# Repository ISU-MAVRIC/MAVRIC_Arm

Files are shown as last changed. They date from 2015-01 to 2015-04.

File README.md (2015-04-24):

# MAVRIC_Arm
The MAVRIC Arm consists of a rotating base (stepper motor), 'shoulder' actuator (with feedback), 'elbow' actuator (with feedback), and an end effector. The end effector is modular but at its maximum contains a rotation servo, horizontal servo, vertical servo, and gripping servo. This board interfaces with the MAVRIC main board, receiving control packets and sending back status packets.

**Features**
- 4 7.4V 5A Buck Regulators powering the high power end effector servos
  - Current measurement on every power output to prevent overheating of both the regulators and the servos themselves
- 3V3 and 5V Buck Regulators powering the STM32 and an external Raspberry Pi
- Powered by single 12V battery rail
- STM32 communicating over RS-485 with the MAVRIC main board for control/status transmission
- STM32 generating PWM to control the actuator drivers, servos, and stepper driver

## Arm Board Prototype 1 Ordered:
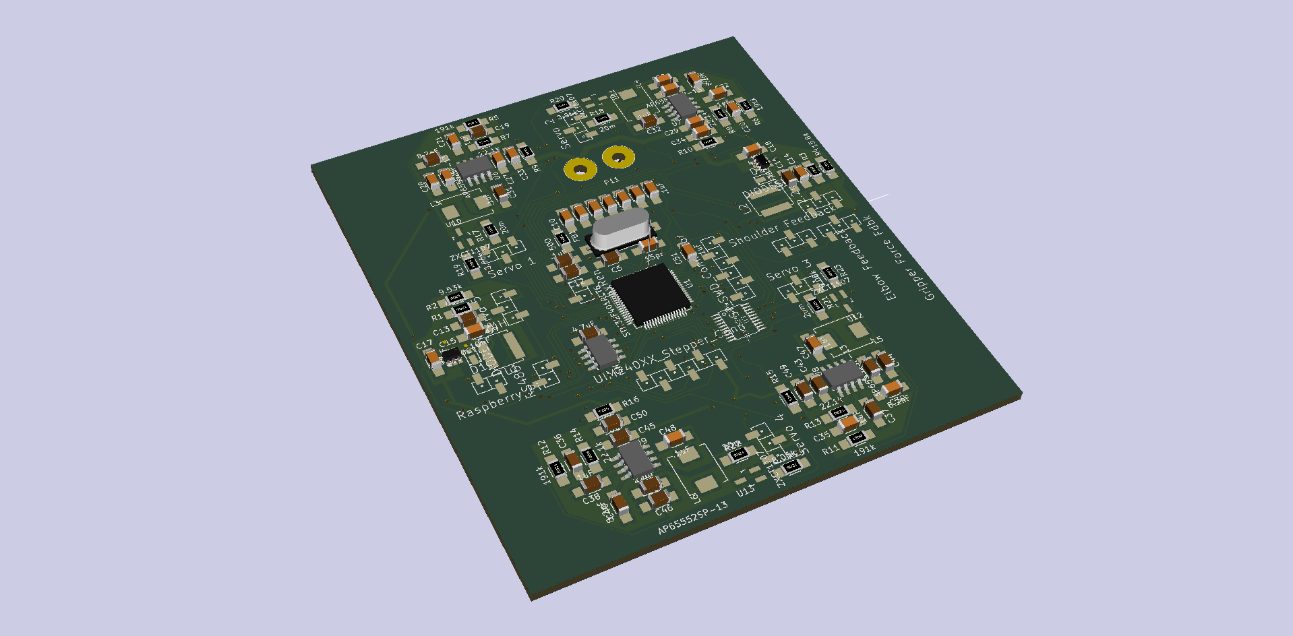
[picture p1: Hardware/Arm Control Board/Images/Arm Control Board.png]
Board 3D


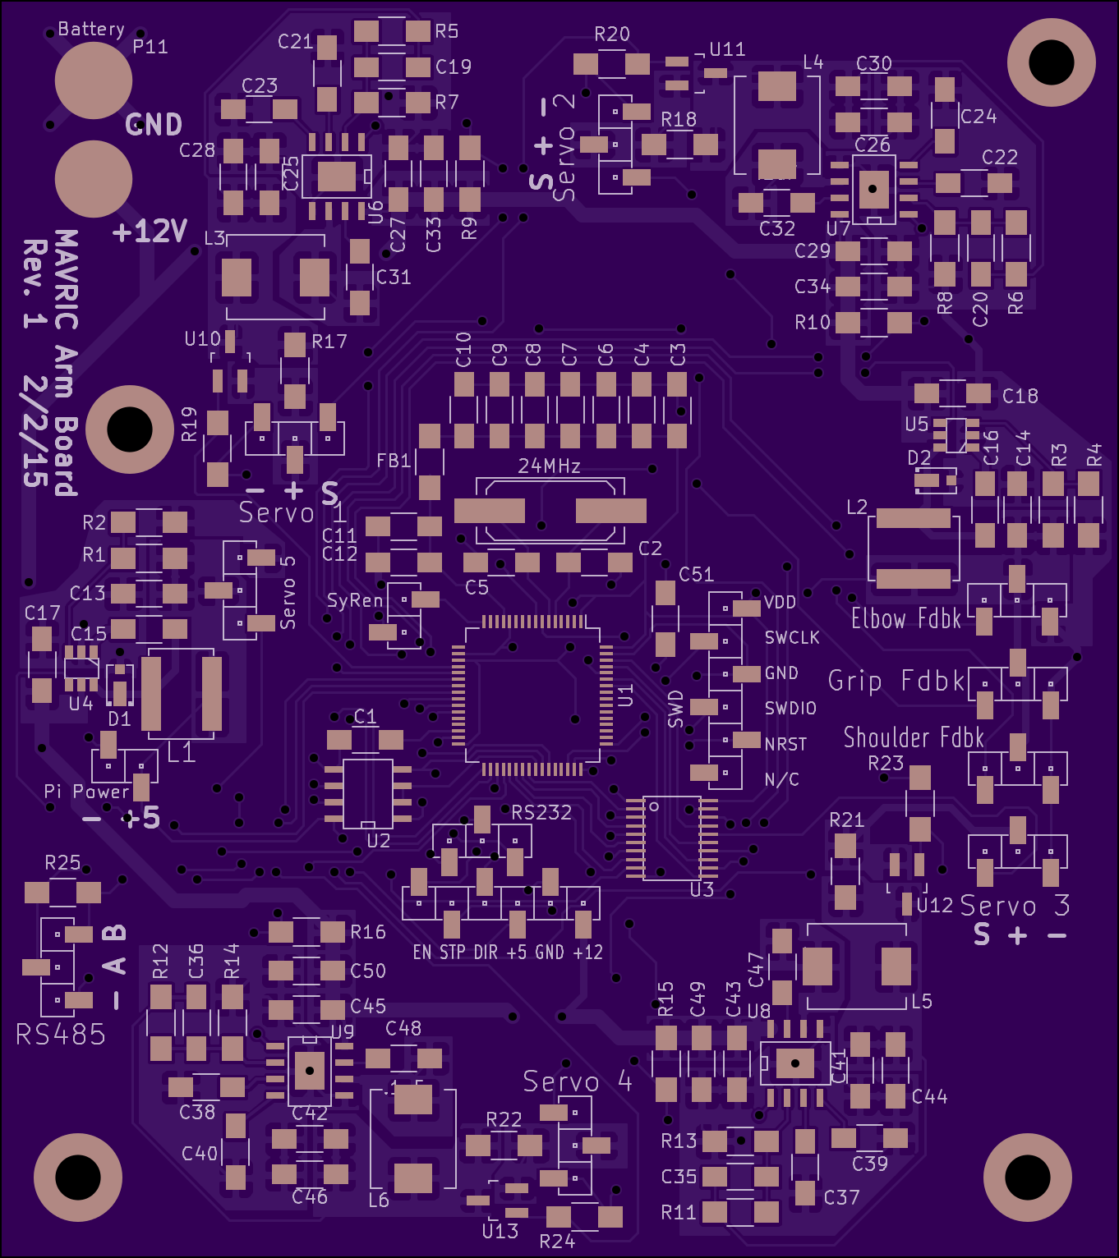
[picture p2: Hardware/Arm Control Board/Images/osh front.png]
Arm Board Front
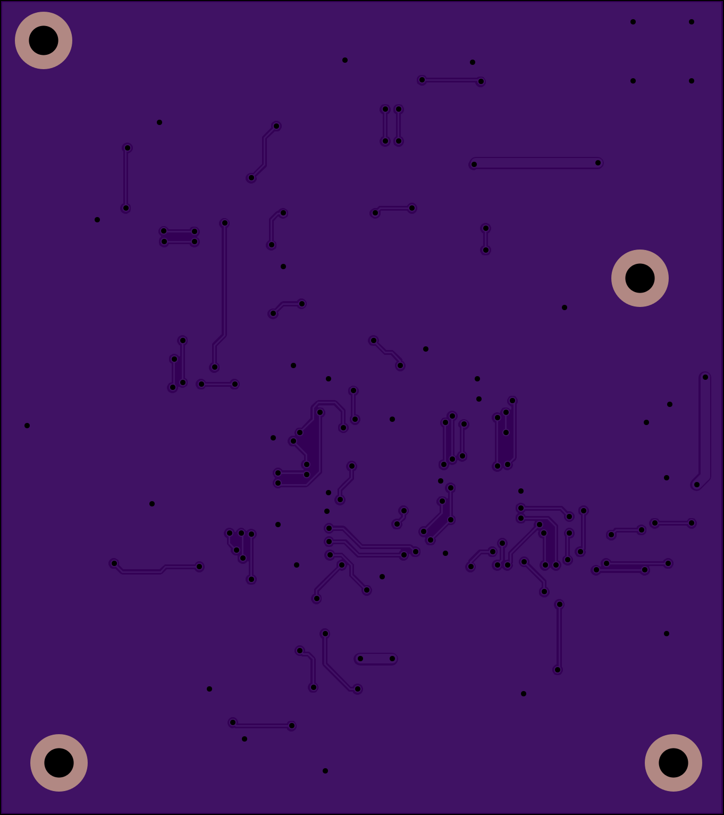
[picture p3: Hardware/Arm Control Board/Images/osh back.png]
Arm Board Back


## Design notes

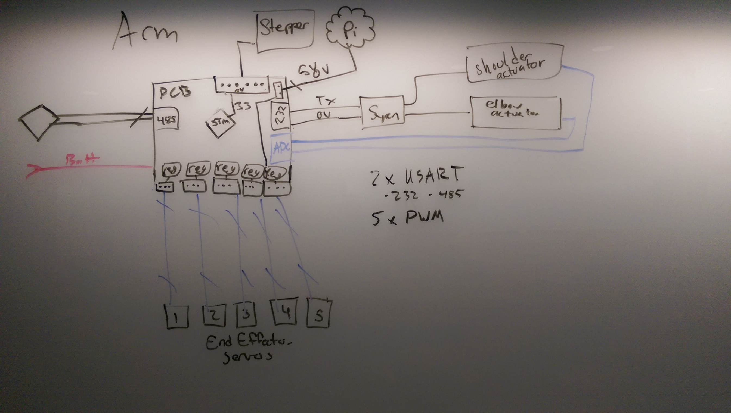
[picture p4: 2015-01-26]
Hardware/Whiteboard Layout.jpg

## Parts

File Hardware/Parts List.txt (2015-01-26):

*Micro*
STM32F401RCT6
*Regulator*
AZ34063UMTR-G1 (Only 1.2A)
AP65552SP-13 (5A sustained)
*RS485 Transceiver*
ST485CDR - More expensive
SN75176BDR - from TI, less expensive

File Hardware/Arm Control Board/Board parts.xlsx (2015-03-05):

Number | Qty | Description
952-1951-ND | 13 | 8POS SIL VERTICAL SMT HEADER
952-2001-ND | 2 | 8POS SIL VERTICAL SMT HEADER
97-14047-ND | 1 | IC MCU ARM M4 32BIT RISC 64LQFP
296-1275-1-ND | 1 | IC DIFF BUS TXCVR 8-SOIC
887-2439-1-ND | 1 | CRYSTAL 24.000MHZ 12PF SMD
568-8329-5-ND | 1 | IC BUFF/DVR TRI-ST DUAL 20TSSOP
AP65552SP-13DICT-ND | 4 | IC REG BUCK ADJ 5A SO-8
ZXCT1107SA-7DICT-ND | 4 | IC CURR MONITOR HIGH SIDE SOT23
785-1277-1-ND | 2 | IC REG BUCK ADJ 1.2A SOT23-6
240-2412-1-ND | 1 | FB1
1276-2854-1-ND | 12 | C3 C4 C6 C8 C9 C10 C11 C51 C31 C32 C47 C48
587-2254-1-ND | 4 | C7 C1 C18 C17
399-8148-1-ND | 5 | C12 C21 C22 C37 C38
887-2439-1-ND | 1 | X1
1276-2809-1-ND | 2 | C5 C2
P100ECT-ND | 1 | R25
MSS2P3-M3/89AGICT-ND | 2 | D2 D1
587-1353-1-ND | 10 | C14 C13 C27 C33 C29 C34 C43 C49 C45 C50
399-7174-1-ND | 2 | C16 C15
587-2098-1-ND | 2 | L2 L1
311-49.9KFRCT-ND | 2 | R3 R1
311-15.8KFRCT-ND | 1 | R4
311-9.53KFRCT-ND | 1 | R2
311-191KFRCT-ND | 4 | R5 R6 R11 R12
311-22.1KFRCT-ND | 4 | R7 R8 R13 R14
311-1152-1-ND | 4 | C19 C20 C35 C36
311-100KERCT-ND | 4 | R9 R10 R15 R16
311-1211-1-ND | 4 | C23 C24 C39 C40
1276-2728-1-ND | 8 | C28 C25 C30 C26 C44 C41 C46 C42
ASPI-0630LR-3R3M-T15CT-ND | 4 | L3 L4 L5 L6
985-1548-1-ND | 4 | R17 R18 R21 R22
P8.06KFCT-ND | 4 | R19 R20 R23 R24
 | 115

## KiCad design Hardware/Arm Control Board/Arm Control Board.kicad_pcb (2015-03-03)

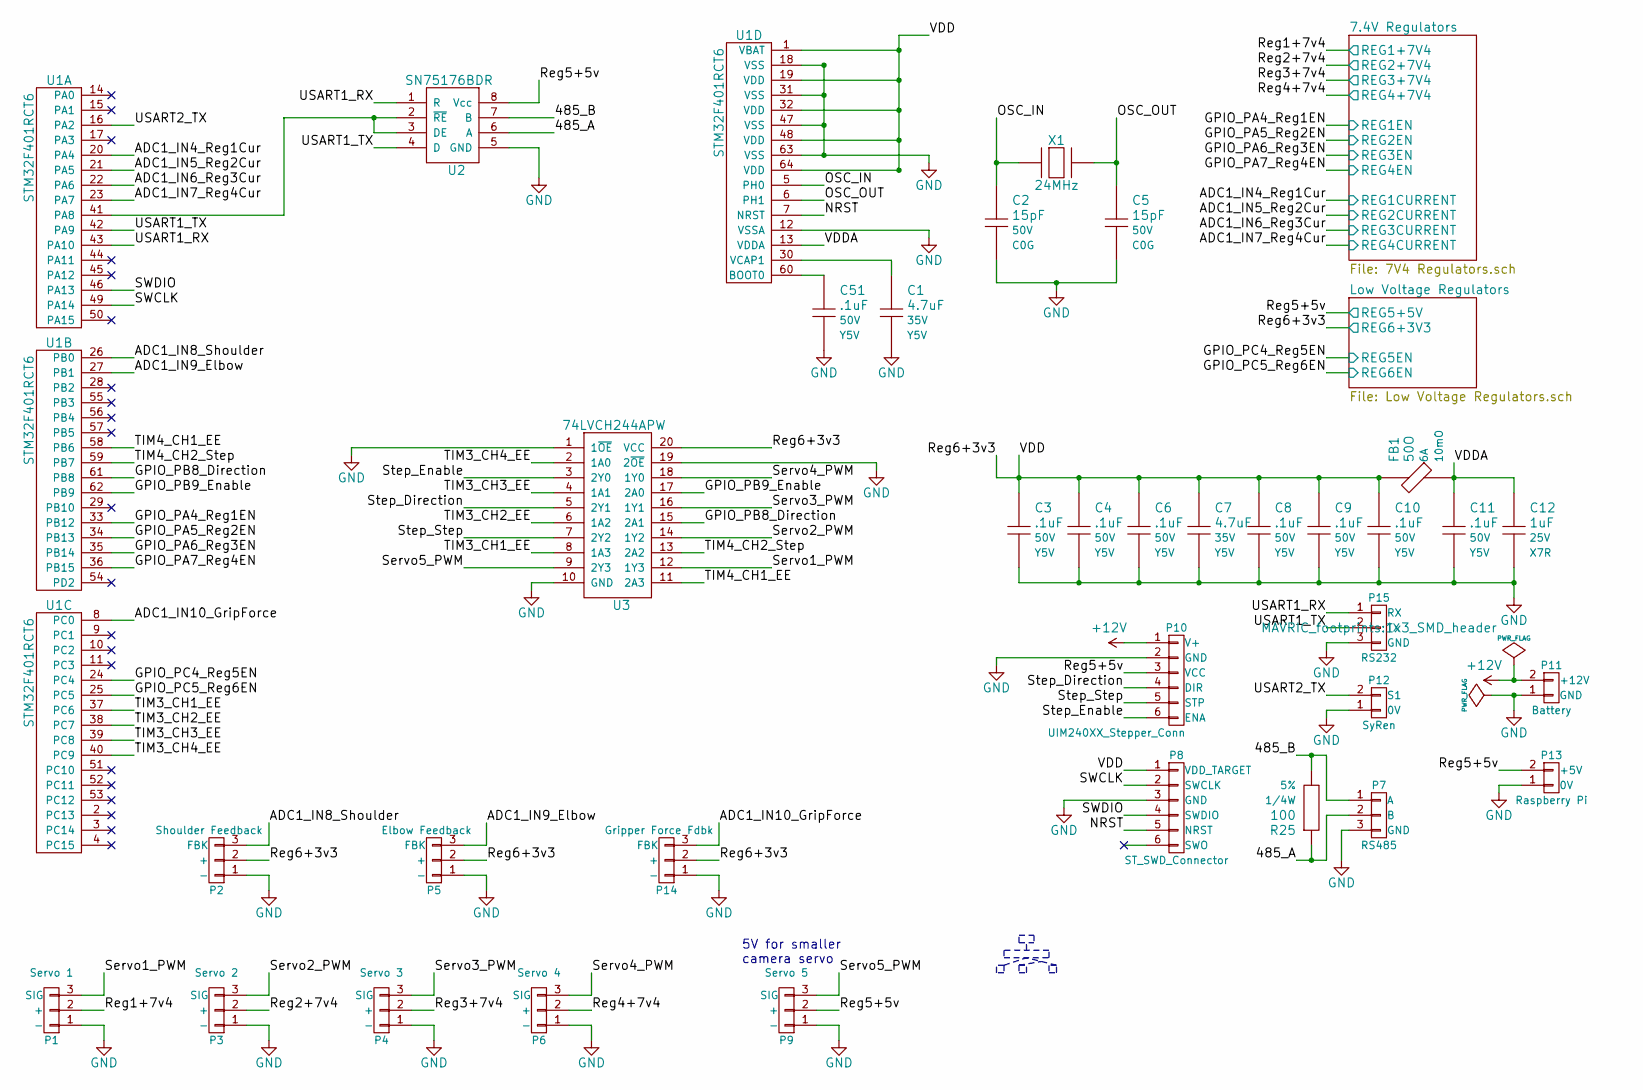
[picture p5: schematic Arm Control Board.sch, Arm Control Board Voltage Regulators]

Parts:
C1, C7: 4.7uF; C_1206_HandSoldering; Voltage 35V; Manufacturer Part # GMK316F475ZG-T
C2, C5: 15pF; C_1206_HandSoldering; Voltage 50V; Manufacturer Part # CL31C150JBCNNNC
C3, C4, C6, C8, C9, C10, C11, C51: .1uF; C_1206_HandSoldering; Voltage 50V; Manufacturer Part # CL31F104MBCNNNC
C12: 1uF; C_1206_HandSoldering; Voltage 25V; Manufacturer Part # C1206C105M3RACTU
FB1: 50O; R_1206_HandSoldering; Manufacturer Part # HI1206T500R-10
P1: Servo 1; 1x3_SMD_header
P2: Shoulder Feedback; 1x3_SMD_header
P3: Servo 2; 1x3_SMD_header
P4: Servo 3; 1x3_SMD_header
P5: Elbow Feedback; 1x3_SMD_header
P6: Servo 4; 1x3_SMD_header
P7: RS485; 1x3_SMD_header
P8: ST_SWD_Connector; 1x6_SMD_header
P9: Servo 5; 1x3_SMD_header
P10: UIM240XX_Stepper_Conn; 1x6_SMD_header
P11: Battery; SolderWirePad_2x_2-5mmDrill
P12: SyRen; 1x2_SMD_header
P13: Raspberry Pi; 1x2_SMD_header
P14: Gripper Force Fdbk; 1x3_SMD_header
P15: RS232; 1x3_SMD_header
R25: 100; R_1206_HandSoldering; Tolerance 5%; Manufacturer Part # ERJ-8GEYJ101V
U1: STM32F401RCT6; LQFP-64_10x10mm_Pitch0.5mm
U2: SN75176BDR; SOIC-8-W
U3: 74LVCH244APW; AB2_TSSOP20
X1: 24MHz; Q_49U3HMS; Tolerance 30ppm; Manufacturer Part # 9C-24.000MAAE-T; Digi-Key Value

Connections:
+12V: P10.1 (V+), P11.2 (+12V); also elsewhere on the board
/7.4V Regulators/REG1+7V4: P1.2 (+); also elsewhere on the board
/7.4V Regulators/REG1CURRENT: U1.20 (PA4); also elsewhere on the board
/7.4V Regulators/REG1EN: U1.33 (PB12); also elsewhere on the board
/7.4V Regulators/REG2+7V4: P3.2 (+); also elsewhere on the board
/7.4V Regulators/REG2CURRENT: U1.21 (PA5); also elsewhere on the board
/7.4V Regulators/REG2EN: U1.34 (PB13); also elsewhere on the board
/7.4V Regulators/REG3+7V4: P4.2 (+); also elsewhere on the board
/7.4V Regulators/REG3CURRENT: U1.22 (PA6); also elsewhere on the board
/7.4V Regulators/REG3EN: U1.35 (PB14); also elsewhere on the board
/7.4V Regulators/REG4+7V4: P6.2 (+); also elsewhere on the board
/7.4V Regulators/REG4CURRENT: U1.23 (PA7); also elsewhere on the board
/7.4V Regulators/REG4EN: U1.36 (PB15); also elsewhere on the board
/485_A: P7.2 (B), R25.1, U2.6 (A)
/485_B: P7.1 (A), R25.2, U2.7 (B)
/ADC1_IN8_Shoulder: P2.3 (FBK), U1.26 (PB0)
/ADC1_IN9_Elbow: P5.3 (FBK), U1.27 (PB1)
/ADC1_IN10_GripForce: P14.3 (FBK), U1.8 (PC0)
/GPIO_PB8_Direction: U1.61 (PB8), U3.15 (2A1)
/GPIO_PB9_Enable: U1.62 (PB9), U3.17 (2A0)
/Low Voltage Regulators/REG5+5V: P9.2 (+), P10.3 (VCC), P13.2 (+5V), U2.8 (Vcc); also elsewhere on the board
/Low Voltage Regulators/REG5EN: U1.24 (PC4); also elsewhere on the board
/Low Voltage Regulators/REG6+3V3: C3.1, C4.1, C6.1, C7.1, C8.1, C9.1, C10.1, FB1.1, P2.2 (+), P5.2 (+), P8.1 (VDD_TARGET), P14.2 (+), U1.1 (VBAT), U1.19 (VDD), U1.32 (VDD), U1.48 (VDD), U1.64 (VDD), U3.20 (VCC); also elsewhere on the board
/Low Voltage Regulators/REG6EN: U1.25 (PC5); also elsewhere on the board
/NRST: P8.5 (NRST), U1.7 (NRST)
/OSC_IN: C2.1, U1.5 (PH0), X1.1
/OSC_OUT: C5.1, U1.6 (PH1), X1.2
/SWCLK: P8.2 (SWCLK), U1.49 (PA14)
/SWDIO: P8.4 (SWDIO), U1.46 (PA13)
/Servo1_PWM: P1.3 (SIG), U3.12 (1Y3)
/Servo2_PWM: P3.3 (SIG), U3.14 (1Y2)
/Servo3_PWM: P4.3 (SIG), U3.16 (1Y1)
/Servo4_PWM: P6.3 (SIG), U3.18 (1Y0)
/Servo5_PWM: P9.3 (SIG), U3.9 (2Y3)
/Step_Direction: P10.4 (DIR), U3.5 (2Y1)
/Step_Enable: P10.6 (ENA), U3.3 (2Y0)
/Step_Step: P10.5 (STP), U3.7 (2Y2)
/TIM3_CH1_EE: U1.37 (PC6), U3.8 (1A3)
/TIM3_CH2_EE: U1.38 (PC7), U3.6 (1A2)
/TIM3_CH3_EE: U1.39 (PC8), U3.4 (1A1)
/TIM3_CH4_EE: U1.40 (PC9), U3.2 (1A0)
/TIM4_CH1_EE: U1.58 (PB6), U3.11 (2A3)
/TIM4_CH2_Step: U1.59 (PB7), U3.13 (2A2)
/USART1_RX: P15.1 (RX), U1.43 (PA10), U2.1 (R)
/USART1_TX: P15.2 (TX), U1.42 (PA9), U2.4 (D)
/USART2_TX: P12.2 (S1), U1.16 (PA2)
/VDDA: C11.1, C12.1, FB1.2, U1.13 (VDDA)
GND: C1.2, C2.2, C3.2, C4.2, C5.2, C6.2, C7.2, C8.2, C9.2, C10.2, C11.2, C12.2, C51.2, P1.1 (-), P2.1 (-), P3.1 (-), P4.1 (-), P5.1 (-), P6.1 (-), P7.3 (GND), P8.3 (GND), P9.1 (-), P10.2 (GND), P11.1 (GND), P12.1 (0V), P13.1 (0V), P14.1 (-), P15.3 (GND), U1.12 (VSSA), U1.18 (VSS), U1.31 (VSS), U1.47 (VSS), U1.63 (VSS), U2.5 (GND), U3.1 (1~OE), U3.10 (GND), U3.19 (2~OE); also elsewhere on the board
unnamed: C1.1, U1.30 (VCAP1)
unnamed: C51.1, U1.60 (BOOT0)
unnamed: U1.41 (PA8), U2.2 (~RE), U2.3 (DE)

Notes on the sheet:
5V for smaller camera servo

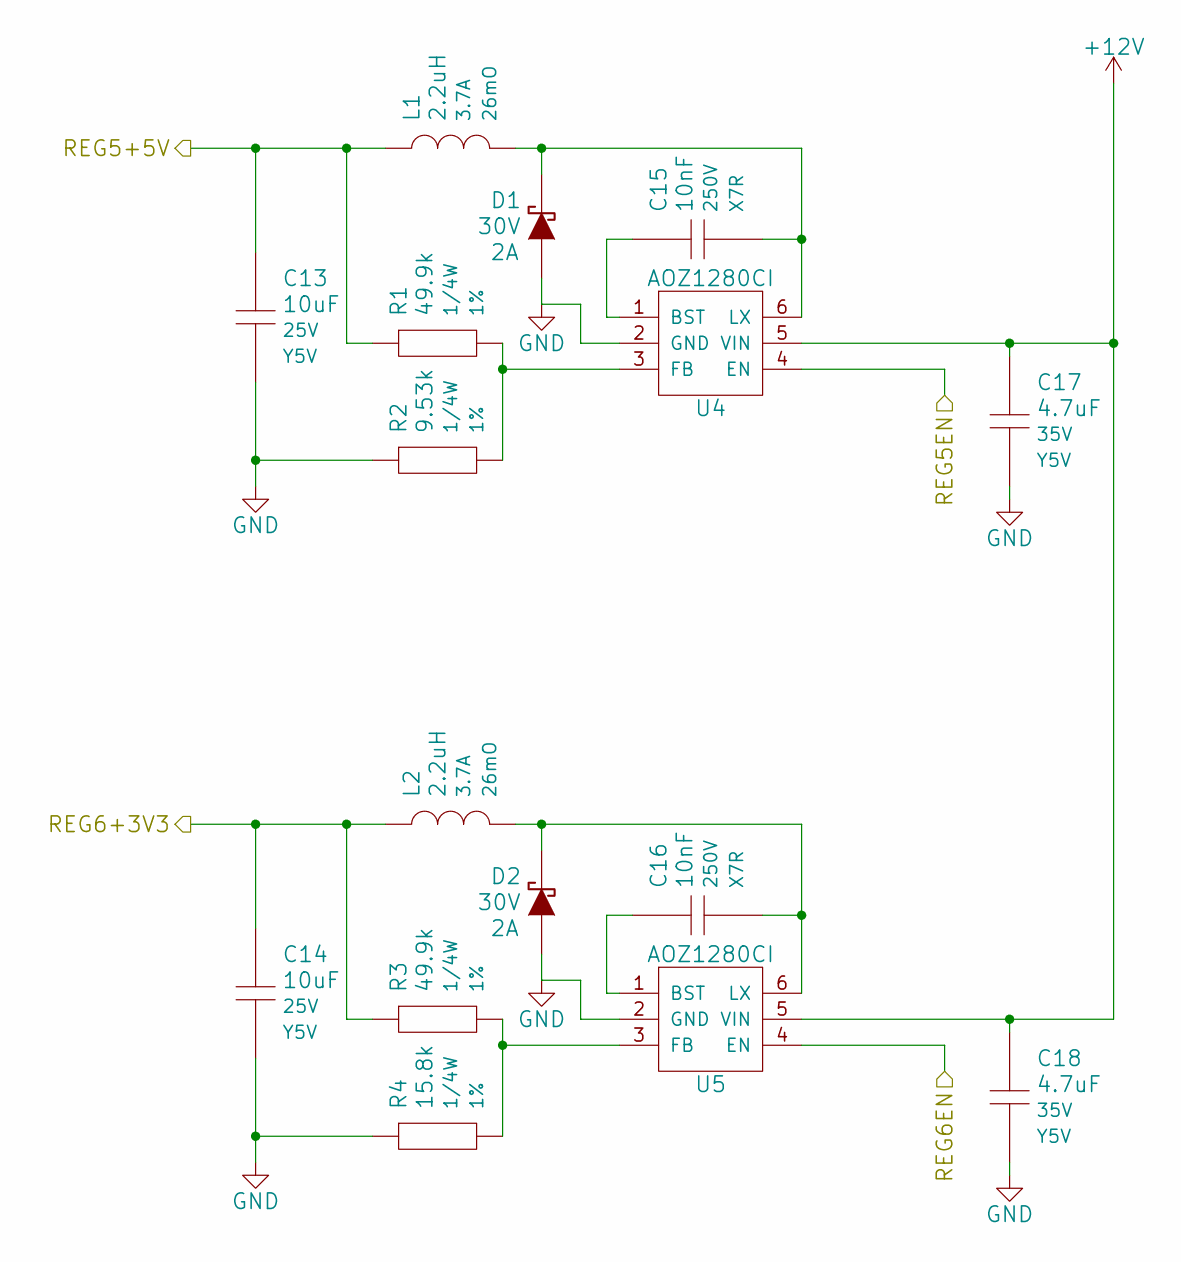
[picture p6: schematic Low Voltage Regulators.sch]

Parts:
C13, C14: 10uF; C_1206_HandSoldering; Voltage 25V; Manufacturer Part # TMK316F106ZL-T
C15, C16: 10nF; C_1206_HandSoldering; Voltage 250V; Manufacturer Part # C1206C103JARACTU; Digi-Key Value
C17, C18: 4.7uF; C_1206_HandSoldering; Voltage 35V; Manufacturer Part # GMK316F475ZG-T
D1, D2: DIODESCH; Diode_MicroSMP; Reverse Voltage 30V; Manufacturer Part # MSS2P3-M3/89A
L1, L2: 2.2uH; Yuden_SMD_Power_Inductor_6060; Manufacturer Part # NR6028T2R2N
R1, R3: 49.9k; R_1206_HandSoldering; Tolerance 1%; Manufacturer Part # RC1206FR-0749K9L
R2: 9.53k; R_1206_HandSoldering; Tolerance 1%; Manufacturer Part # RC1206FR-079K53L
R4: 15.8k; R_1206_HandSoldering; Tolerance 1%; Manufacturer Part # RC1206FR-0715K8L
U4, U5: AOZ1280CI; SOT-23-6

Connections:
+12V: C17.1, C18.1, U4.5 (VIN), U5.5 (VIN); also elsewhere on the board
/Low Voltage Regulators/REG5+5V: C13.1, L1.1, R1.1; also elsewhere on the board
/Low Voltage Regulators/REG5EN: U4.4 (EN); also elsewhere on the board
/Low Voltage Regulators/REG6+3V3: C14.1, L2.1, R3.1; also elsewhere on the board
/Low Voltage Regulators/REG6EN: U5.4 (EN); also elsewhere on the board
GND: C13.2, C14.2, C17.2, C18.2, D1.1 (A), D2.1 (A), R2.1, R4.1, U4.2 (GND), U5.2 (GND); also elsewhere on the board
unnamed: C15.1, U4.1 (BST)
unnamed: C15.2, D1.2 (K), L1.2, U4.6 (LX)
unnamed: C16.1, U5.1 (BST)
unnamed: C16.2, D2.2 (K), L2.2, U5.6 (LX)
unnamed: R1.2, R2.2, U4.3 (FB)
unnamed: R3.2, R4.2, U5.3 (FB)

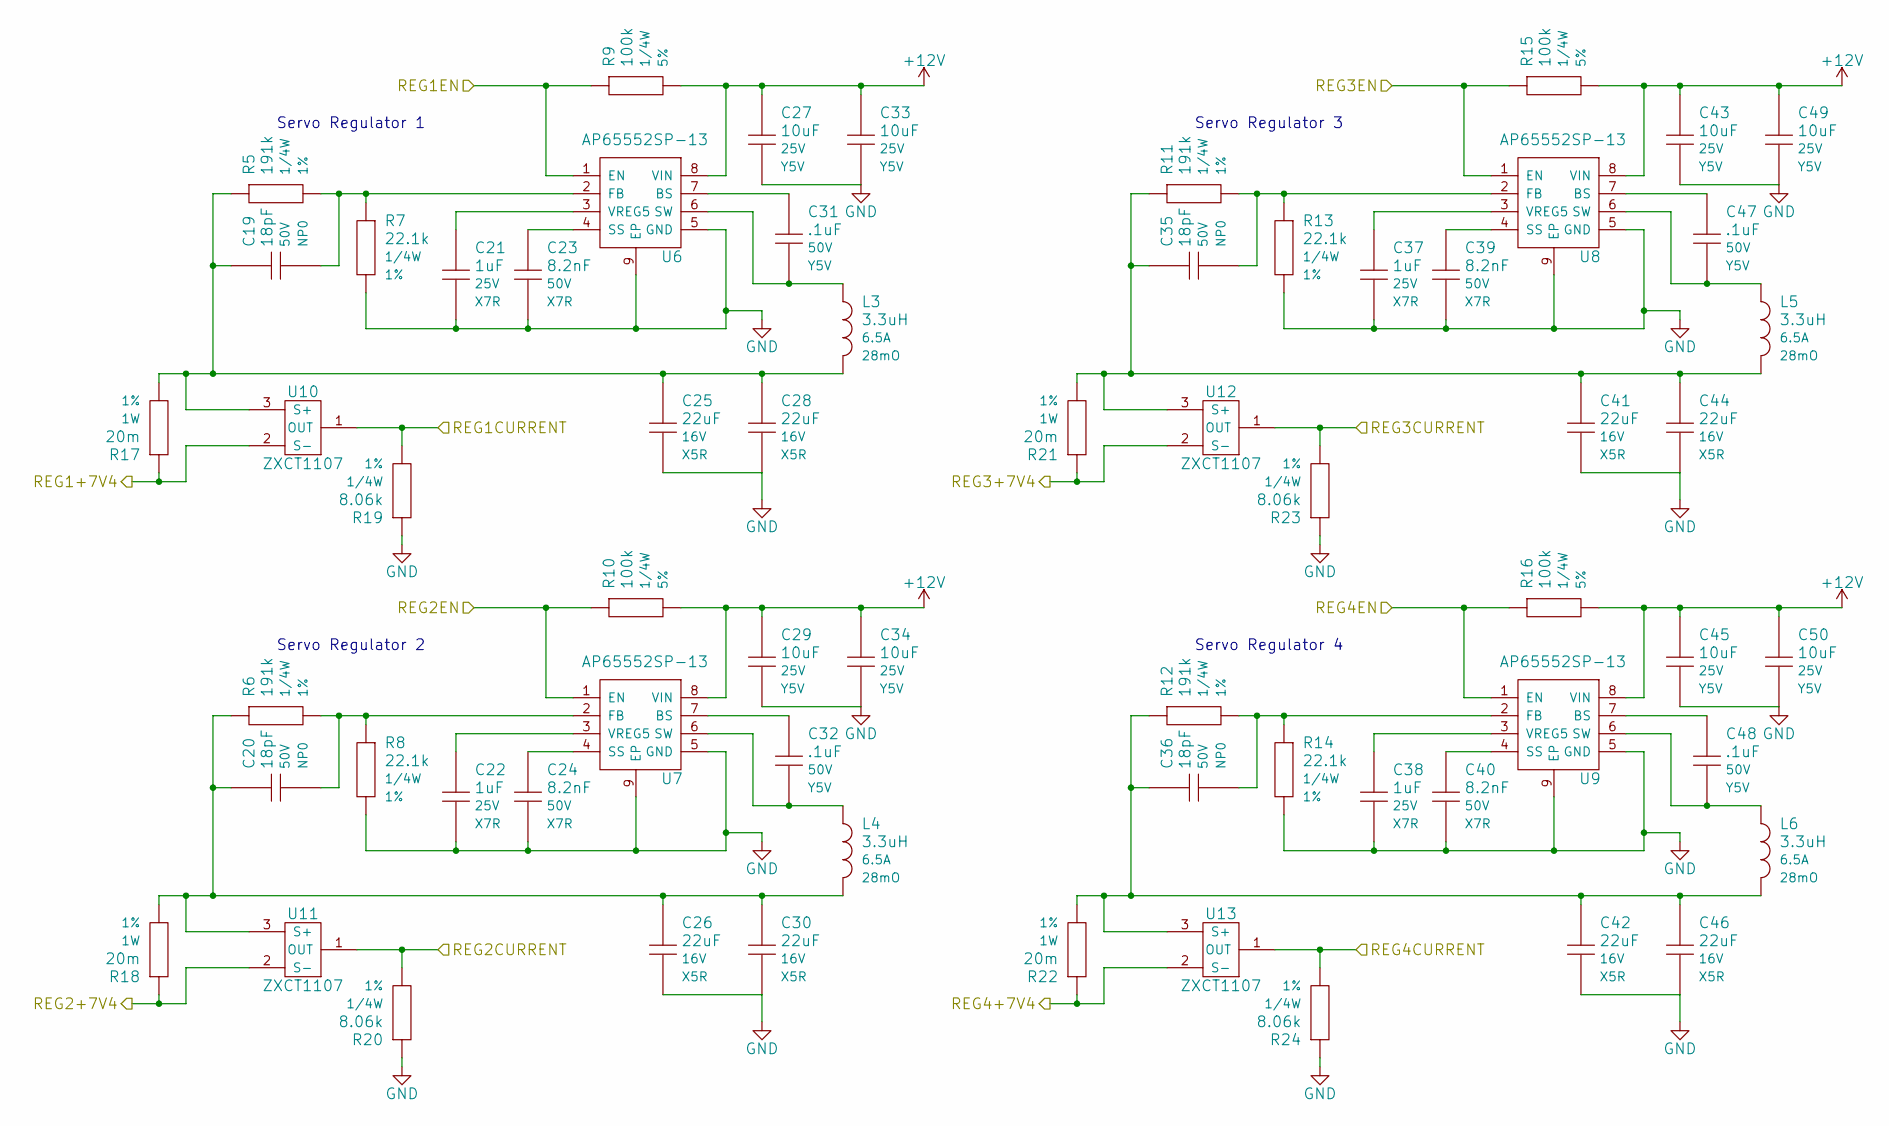
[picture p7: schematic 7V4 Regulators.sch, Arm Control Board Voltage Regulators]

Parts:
C19, C20, C35, C36: 18pF; C_1206_HandSoldering; Voltage 50V; Manufacturer Part # CC1206JRNPO9BN180
C21, C22, C37, C38: 1uF; C_1206_HandSoldering; Voltage 25V; Manufacturer Part # C1206C105M3RACTU
C23, C24, C39, C40: 8.2nF; C_1206_HandSoldering; Voltage 50V; Manufacturer Part # CC1206KRX7R9BB822
C25, C26, C28, C30, C41, C42, C44, C46: 22uF; C_1206_HandSoldering; Voltage 16V; Manufacturer Part # CL31A226MOCLNNC
C27, C29, C33, C34, C43, C45, C49, C50: 10uF; C_1206_HandSoldering; Voltage 25V; Manufacturer Part # TMK316F106ZL-T
C31, C32, C47, C48: .1uF; C_1206_HandSoldering; Voltage 50V; Manufacturer Part # CL31F104MBCNNNC
L3, L4, L5, L6: 3.3uH; Neosid_Inductor_SM-PIC0612H; Manufacturer Part # ASPI-0630LR-3R3M-T15
R5, R6, R11, R12: 191k; R_1206_HandSoldering; Tolerance 1%; Manufacturer Part # RC1206FR-07191KL
R7, R8, R13, R14: 22.1k; R_1206_HandSoldering; Tolerance 1%; Manufacturer Part # RC1206FR-0722K1L
R9, R10, R15, R16: 100k; R_1206_HandSoldering; Tolerance 5%; Manufacturer Part # RC1206JR-07100KL
R17, R18, R21, R22: 20m; R_1206_HandSoldering; Tolerance 1%; Manufacturer Part # LRMAM1206-R02FT5
R19, R20, R23, R24: 8.06k; R_1206_HandSoldering; Tolerance 1%; Manufacturer Part # ERJ-8ENF8061V
U6, U7, U8, U9: AP65552SP-13; SOIC-8-N-1EP
U10, U11, U12, U13: ZXCT1107; SOT23_Transistor_Handsoldering_RevB_14Mar2014

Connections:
+12V: C27.1, C29.1, C33.1, C34.1, C43.1, C45.1, C49.1, C50.1, R9.2, R10.2, R15.2, R16.2, U6.8 (VIN), U7.8 (VIN), U8.8 (VIN), U9.8 (VIN); also elsewhere on the board
/7.4V Regulators/REG1+7V4: R17.1, U10.2 (S-); also elsewhere on the board
/7.4V Regulators/REG1CURRENT: R19.2, U10.1 (OUT); also elsewhere on the board
/7.4V Regulators/REG1EN: R9.1, U6.1 (EN); also elsewhere on the board
/7.4V Regulators/REG2+7V4: R18.1, U11.2 (S-); also elsewhere on the board
/7.4V Regulators/REG2CURRENT: R20.2, U11.1 (OUT); also elsewhere on the board
/7.4V Regulators/REG2EN: R10.1, U7.1 (EN); also elsewhere on the board
/7.4V Regulators/REG3+7V4: R21.1, U12.2 (S-); also elsewhere on the board
/7.4V Regulators/REG3CURRENT: R23.2, U12.1 (OUT); also elsewhere on the board
/7.4V Regulators/REG3EN: R15.1, U8.1 (EN); also elsewhere on the board
/7.4V Regulators/REG4+7V4: R22.1, U13.2 (S-); also elsewhere on the board
/7.4V Regulators/REG4CURRENT: R24.2, U13.1 (OUT); also elsewhere on the board
/7.4V Regulators/REG4EN: R16.1, U9.1 (EN); also elsewhere on the board
GND: C21.2, C22.2, C23.2, C24.2, C25.2, C26.2, C27.2, C28.2, C29.2, C30.2, C33.2, C34.2, C37.2, C38.2, C39.2, C40.2, C41.2, C42.2, C43.2, C44.2, C45.2, C46.2, C49.2, C50.2, R7.2, R8.2, R13.2, R14.2, R19.1, R20.1, R23.1, R24.1, U6.5 (GND), U6.9 (EP), U7.5 (GND), U7.9 (EP), U8.5 (GND), U8.9 (EP), U9.5 (GND), U9.9 (EP); also elsewhere on the board
unnamed: C19.1, C25.1, C28.1, L3.2, R5.1, R17.2, U10.3 (S+)
unnamed: C19.2, R5.2, R7.1, U6.2 (FB)
unnamed: C20.1, C26.1, C30.1, L4.2, R6.1, R18.2, U11.3 (S+)
unnamed: C20.2, R6.2, R8.1, U7.2 (FB)
unnamed: C21.1, U6.3 (VREG5)
unnamed: C22.1, U7.3 (VREG5)
unnamed: C23.1, U6.4 (SS)
unnamed: C24.1, U7.4 (SS)
unnamed: C31.1, U6.7 (BS)
unnamed: C31.2, L3.1, U6.6 (SW)
unnamed: C32.1, U7.7 (BS)
unnamed: C32.2, L4.1, U7.6 (SW)
unnamed: C35.1, C41.1, C44.1, L5.2, R11.1, R21.2, U12.3 (S+)
unnamed: C35.2, R11.2, R13.1, U8.2 (FB)
unnamed: C36.1, C42.1, C46.1, L6.2, R12.1, R22.2, U13.3 (S+)
unnamed: C36.2, R12.2, R14.1, U9.2 (FB)
unnamed: C37.1, U8.3 (VREG5)
unnamed: C38.1, U9.3 (VREG5)
unnamed: C39.1, U8.4 (SS)
unnamed: C40.1, U9.4 (SS)
unnamed: C47.1, U8.7 (BS)
unnamed: C47.2, L5.1, U8.6 (SW)
unnamed: C48.1, U9.7 (BS)
unnamed: C48.2, L6.1, U9.6 (SW)

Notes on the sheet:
Servo Regulator 1
Servo Regulator 2
Servo Regulator 3
Servo Regulator 4

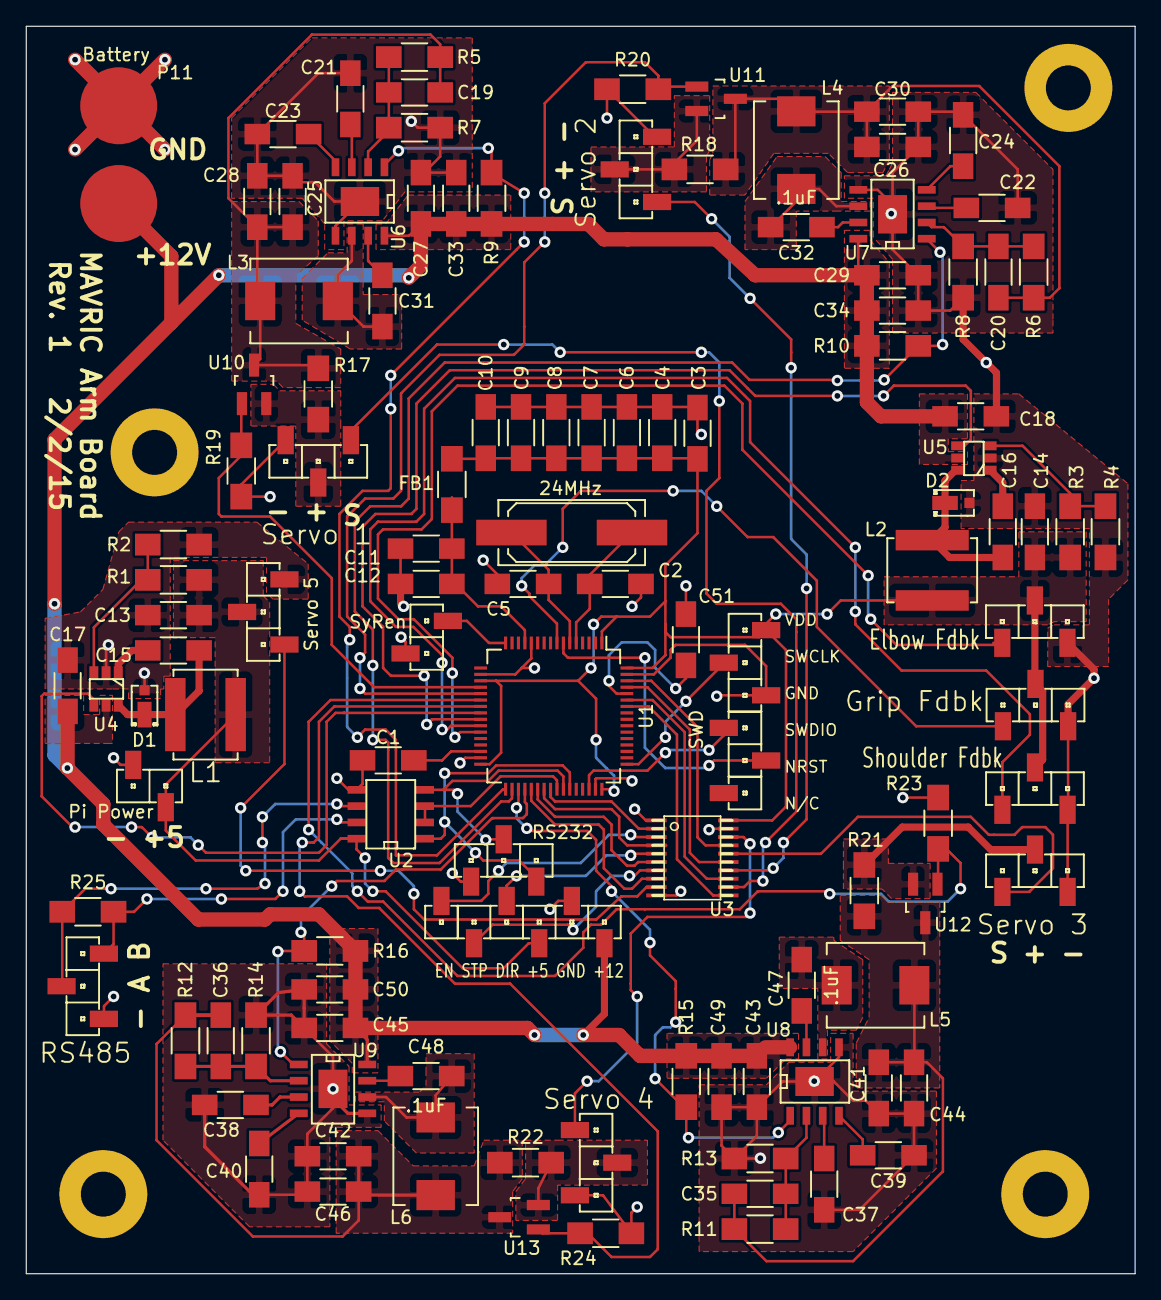
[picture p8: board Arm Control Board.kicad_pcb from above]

Board: 2 copper layers, 86.4 x 97.2 mm, 118 parts (0 on the bottom side), 81 nets.

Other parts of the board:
MountingHole_3-5mm, MountingHole_3-5mm#2, MountingHole_3-5mm#3, MountingHole_3-5mm#4: VAL**; PlatedMountingHole_3-5mm

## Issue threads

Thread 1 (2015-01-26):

Add programming/debugging connections to STM32

markrusciano, 2015-01-26:
Good info here:http://www.micromouseonline.com/2011/11/05/stlink-swd-for-stm32/

Might need to move around GPIO for power supply enable pins

markrusciano, 2015-01-28:
SWD port added

Closed 2015-01-28.

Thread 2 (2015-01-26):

Add connection and regulator for stepper motor and driver

markrusciano, 2015-01-26:
Driver: UIM24004T
http://machmo.com/stepperdrivers/UIM24004T.html

markrusciano, 2015-01-28:
Connector added, all six pins are in one connector for now. We'll see if that causes any problems.

Closed 2015-01-28.

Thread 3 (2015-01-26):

Add ADC connections for arm actuator feedback

markrusciano, 2015-01-26:
Pinout here: https://www.servocity.com/html/180_lbs__thrust_linear_actuato.html#.VMWnL_7F98E

markrusciano, 2015-01-28:
connectors created and added to schematic

Closed 2015-01-28.

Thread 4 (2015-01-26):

Find better solution for servo PWM over long runs

markrusciano, 2015-01-26:
Options:

* Sink 5V into STM32
* Buffer IC

markrusciano, 2015-01-26:
1 Channel: 74LVC1G17SE-7
8 Channel: 74LVCH244APW,118

markrusciano, 2015-01-28:
8 channel 74LVCH244APW,112 part created and added to schematic.

Closed 2015-01-28.

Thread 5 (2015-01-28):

Add external oscillator for STM32

markrusciano, 2015-01-28:
Might add some precision for the touchy PWM signals. May be entirely unnecessary

markrusciano, 2015-01-30:
added

Closed 2015-01-30.

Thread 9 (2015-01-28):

Review connector design for max current and signal interference

markrusciano, 2015-01-28:

markrusciano, 2015-01-30:
not needed until board tested

Closed 2015-01-30.

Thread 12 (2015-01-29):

Raspberry Pi needs separate regulator for 5V

markrusciano, 2015-01-29:

markrusciano, 2015-01-29:
Servo 5 regulator is now 5V. If a camera tilt servo is required, it won't need 7.4 like the others.

Closed 2015-01-29.

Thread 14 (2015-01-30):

create document listing ICs with components that need to be close

markrusciano, 2015-01-30:
many ICs have caps between their 12V input and ground. This isn't really designated too well in pcbnew. This will avoid having an AOZ cap sitting by an AP.

markrusciano, 2015-01-31:
looking at the schematic printout works just fine when it's before midnight

Closed 2015-01-31.

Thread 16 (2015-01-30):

double check custom footprint pads and component outlines

markrusciano, 2015-01-30:
not about to have components running into each other/not fitting on their pads

Closed 2015-03-03.

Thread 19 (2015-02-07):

Verify STM32 part is pin correct

markrusciano, 2015-02-07:

Closed 2015-02-08.

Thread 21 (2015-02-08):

Final Checklist before Fab

markrusciano, 2015-02-08:
- [x] Verify all parts have correct pin names and numbers
- [x] Verify connections to parts match datasheet/pin designations

Will be adding more items...

Closed 2015-03-03.

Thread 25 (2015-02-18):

Pudding

ethanharstad, 2015-02-18:
Pudding is a critical lubricant for the proper functioning of the engineers. We need more.

markrusciano, 2015-02-18:
[ ] create MAVRIC_Pantry repo for addressing critical issues of sustinance

JDD314, 2015-02-18:
Lol

markrusciano, 2015-02-18:
With 17, 5 Star reviews, I am making an official recommendation of the Cafe Classics Chocolate 6 Pack
http://www.webstaurantstore.com/cafe-classics-a1rfd12d-chocolate-pudding-6-10-cans-case/108A1RFD12D.html

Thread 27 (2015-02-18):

Code in all of our PWM objects

markrusciano, 2015-02-18:
Using the mbed PwmOut library (http://developer.mbed.org/handbook/PwmOut), create a PwmOut object for every PWM device we will have connected to the MAVRIC_Arm Board

Example:
PwmOut arm_elbow(PA_7);

PWM Connections

Device | Pin
---------|-------
Stepper Step | PB_7
Servo 1 | PC_6
Servo 2 | PC_7
Servo 3 | PC_8
Servo 4 | PC_9
Servo 5 | PB_6

If the mbed stuff is confusing, I'd recommend going through this tutorial here:
https://learn.sparkfun.com/tutorials/mbed-starter-kit-experiment-guide/experiment-2-buttons-and-pwm
Make sure to type the code, don't just copy paste. It has helped me a lot.

Use the old mbed code for reference if you'd like
https://github.com/ISU-MAVRIC/MAVRIC_Main/blob/master/Firmware/MAVRIC_Main/main.cpp

zdanger, 2015-02-20:
http://developer.mbed.org/users/zadanger/code/arm_control_pwm/rev/0f3b03031f63

Closed 2015-02-20.

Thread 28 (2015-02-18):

Create main loop writing to the PWM objects

markrusciano, 2015-02-18:
Reference for PWM out: http://developer.mbed.org/handbook/PwmOut

In your main loop in the mbed project, for each servo object call period_us(20000) to set the PWM outputs to the period servos are compatible with. Then, for each object, call pulsewidth_us(###) with ### being any number from 1000 to 2000. 1000 is 0 degrees on a servo, 2000 is 180 degrees typically.

zdanger, 2015-02-20:
http://developer.mbed.org/users/zadanger/code/arm_control_pwm/rev/713aa5db7af8

Closed 2015-02-20.

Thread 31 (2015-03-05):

Add missing polarity indicators

markrusciano, 2015-03-05:
- [ ] Servo 4
- [ ] Servo 5
- [ ] SyRen Serial
- [ ] RS232

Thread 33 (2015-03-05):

Edit MAVRIC custom parts to have vendor and vendor part number fields

markrusciano, 2015-03-05:
See the Aerodyne Labs KiCad passives library for reference. This will make BOM creation a snap

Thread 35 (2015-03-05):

Rework 12V battery power distribution

markrusciano, 2015-03-05:
Currently the 12V battery power just snakes around the board. I'm thinking there could be a better, cleaner way to do this.

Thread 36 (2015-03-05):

Add current sensing to 5V servo connector

markrusciano, 2015-03-05:
We have it on the other servos, we might as well have it on the 5V servo connector as well as long as we can snag an ADC channel (shouldn't be an issue)

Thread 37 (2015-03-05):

Add current sensing to SyRen

markrusciano, 2015-03-05:
The SyRen just pulls 12V from the battery. For this, we would have the SyRen wired to its own 12V terminal on the arm board with a current sense chip (ZXCT1107) running to the ADC. We won't be able to tell individual arm axis current draws but we will be able to see if one of the two are stalled.

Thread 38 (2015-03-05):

Change SMD Header Pin footprint

markrusciano, 2015-03-05:
The footprint for the current 1x3 and 1x6 and 1x2 headers are for this odd standalone header that you can buy. It is kinda crazy expensive compared to buying a 40 long strip. With this new strip (http://www.digikey.com/product-detail/en/NREC039SABC-M30RC/S1013EC-39-ND/2775095) we will be able to buy strips of 40 and just break them apart. A secondary benefit is they have more board contact area so our plugs won't rip off as easily.

Note: The header footprints are in the MAVRIC_Hardware repository under the KiCad folder

Closed 2015-03-08.

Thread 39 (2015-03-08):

Redesign thermal pad on AP regulators

markrusciano, 2015-03-08:
Soldering the thermal pad of the AP regulators may be pretty difficult. Dave goes over a way that may help us out https://www.youtube.com/watch?v=588iV07nEdM . Essentially you put a bare copper pad directly under the thermal pad connected with a couple of vias to the thermal pad of the chip.

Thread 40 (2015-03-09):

Add cat5 jack for ethernet

markrusciano, 2015-03-09:
Part and footprint exist. Connect in a similar way to the wheel pod board. Only 485 and grounds for now

Closed 2015-03-28.

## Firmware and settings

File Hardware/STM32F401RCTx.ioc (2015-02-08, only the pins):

Mcu.UserName=STM32F401RCTx
PA10.Signal=USART1_RX
PA13.Signal=SYS_JTMS-SWDIO
PA14.Signal=SYS_JTCK-SWCLK
PA2.Signal=USART2_TX
PA3.Signal=USART2_RX
PA4.Signal=ADCx_IN4
PA5.Signal=ADCx_IN5
PA6.Signal=ADCx_IN6
PA7.Signal=ADCx_IN7
PA8.Signal=GPIO_Output
PA9.Signal=USART1_TX
PB0.Signal=ADCx_IN8
PB1.Signal=ADCx_IN9
PB12.Signal=GPIO_Output
PB13.Signal=GPIO_Output
PB14.Signal=GPIO_Output
PB15.Signal=GPIO_Output
PB6.Signal=S_TIM4_CH1
PB7.Signal=S_TIM4_CH2
PB8.Signal=GPIO_Output
PB9.Signal=GPIO_Output
PC0.Signal=ADCx_IN10
PC4.Signal=GPIO_Output
PC5.Signal=GPIO_Output
PC6.Signal=S_TIM3_CH1
PC7.Signal=S_TIM3_CH2
PC8.Signal=S_TIM3_CH3
PC9.Signal=S_TIM3_CH4

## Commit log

2015-01-25 Blank project files added
    [Arm Control Board.kicad_pcb, Arm Control Board.sch]
2015-01-25 Created STM32CubeMX Project
    [Arm Control Board.kicad_pcb, Arm Control Board.sch]
2015-01-25 Added regulator to schematic
    Also added gitignore, parts list, and microcontroller datasheet
    [Arm Control Board.sch]
2015-01-26 Added new AP65552SP-13 regulator circuit
    More current for the servos
    [Arm Control Board.sch]
2015-01-26 Creating servo regulator circuits, datasheets
    [Arm Control Board.sch, Power.sch]
2015-01-26 Added enable pins to all servo regulators
    Might not need them all independent, we'll see
    [Arm Control Board.sch, Power.sch]
2015-01-26 Added and connected servo plugs
    [Arm Control Board.sch, Power.sch]
2015-01-26 Added lower cost 485 Transceiver, connected serial
    [Arm Control Board.sch]
2015-01-26 Added SyRen serial connector
    [Arm Control Board.sch]
2015-01-26 Raspberry Pi power connector + started STM32 power
    [Arm Control Board.sch]
2015-01-28 Added 74LVCH244APW buffer to servo lines
    Able to push much more current than the micro can
    [Arm Control Board.sch]
2015-01-28 Attempt to ignore $ files from KiCad
2015-01-28 Cleaned up schematic, cube, added stepper connector
    [Arm Control Board.sch, Power.sch]
2015-01-28 More clean up, added connector for actuator fbck
    [Arm Control Board.sch, Power.sch]
2015-01-28 Added SWD connector for program/debug
    [Arm Control Board.sch]
2015-01-28 Fixed some floating wires
    [Arm Control Board.sch, Power.sch]
2015-01-29 Reorganized regulators, added 5V reg, ext osc, PNs
    Way too much for one commit, sorry about that. Reorganized the
    regulators into high voltage/low voltage sheets. Added product numbers
    to all passives + more. Check issues for any other changes
    [7V4 Regulators.sch, Arm Control Board.sch, Low Voltage Regulators.sch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]
2015-01-29 More footprints added, components annotated
    [7V4 Regulators.sch, Arm Control Board.sch, Low Voltage Regulators.sch]
2015-01-29 Initial PCB layout
    [7V4 Regulators.sch, Arm Control Board.kicad_pcb, Arm Control Board.sch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]
2015-01-30 all components have footprints assigned now
    [Arm Control Board.sch, Low Voltage Regulators.sch]
2015-01-30 Fixed pin numbers being names
    Crime doesn't pay, kids. If your names aren't showing up on your part,
    don't just make the numbers your names. Find out how to make the names
    show up.
    [Arm Control Board.sch]
2015-01-30 Fixed parts with pin numbers starting at zero
    just a zero indexed man living in a one indexed world
    [Arm Control Board.kicad_pcb, Arm Control Board.sch]
2015-01-30 reg1 layout made
    expecting it to change bunches
    [Arm Control Board.kicad_pcb]
2015-01-30 started reg2 layout
    [Arm Control Board.kicad_pcb]
2015-01-31 Attached BOOT0 and VBAT
    [7V4 Regulators.sch, Arm Control Board.sch, Low Voltage Regulators.sch]
2015-01-31 created a couple of different 7v4 regulator layouts
    [Arm Control Board.kicad_pcb]
2015-01-31 honestly I have no clue but kicad wanted to save
    sorry guys really dropped the ball on this commit
    [7V4 Regulators.sch, Arm Control Board.sch, Low Voltage Regulators.sch]
2015-02-01 adding vias so the ground doesn't com*plane*
    [Arm Control Board.kicad_pcb]
2015-02-02 more vias but to be honest the situation is a mess
    [Arm Control Board.kicad_pcb]
2015-02-07 Added current sensing to reg1-4, updated STMCube
    Only high current servo outputs have current sensing. STMCube was not up
    to date with pin assignments. Issues: #18 #15
    [7V4 Regulators.sch, Arm Control Board.kicad_pcb, Arm Control Board.sch]
2015-02-08 Fixed STM32 Part
    Had extra two VSS + VDD pins that didn't exist. Added PD2 pin. Resolves
    #19
    [Arm Control Board.sch]
2015-02-08 Fixed power connections to STM32
    The part changes screwed some connections up
    [Arm Control Board.sch]
2015-02-08 Added clamp force sensor port in cube and schematic
    Resolves #20
    [Arm Control Board.sch]
2015-02-08 Lay out regulators 1-4, update cube for oscillator
    Got strangely excited about this commit. Almost called my dad...
    [7V4 Regulators.sch, Arm Control Board.kicad_pcb, Arm Control Board.sch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]
2015-02-09 Initial layout of Regulator 5 (AOZ)
    Followed datasheet recommendations pretty well, probably some room for
    improvement
    [7V4 Regulators.sch, Arm Control Board.kicad_pcb]
2015-02-09 Initial layout of Reg 6 (AOZ) and reorg of reg1-4
    [Arm Control Board.kicad_pcb]
2015-02-09 Continuation of board layout. 80% connected
    Very poor layout so far, this will change drastically before fab
    [Arm Control Board.kicad_pcb]
2015-02-09 Reorganize all regulators. Reorganize buffer pins
    Pins reorganized to simplify board flow
    [Arm Control Board.kicad_pcb, Arm Control Board.sch]
2015-02-09 Connecting more things in better ways
    Just in case i screw something up
    [Arm Control Board.kicad_pcb]
2015-02-09 Delete Arm Control Board.kicad_pcb-bak
    Because backups have no place in our repo
2015-02-09 Connect everything but 12V and GND
    Not like those lines are really necessary. MAVRIC is more than capable
    of running off of team spirit, optimism, and enthusiasm.
    [Arm Control Board.kicad_pcb]
2015-02-09 Condensing Stage 1
    Just an intermediate commit in case something goes horribly wrong
    [Arm Control Board.kicad_pcb]
2015-02-09 Condensing Stage 2
    Still in progress, many of the traces are now in reasonable, space
    conservative spots
    [Arm Control Board.kicad_pcb]
2015-02-10 Condensing Stage 3 + Board Outline
    [Arm Control Board.kicad_pcb]
2015-02-10 Complete Layout Revision 1
    [Arm Control Board.kicad_pcb]
2015-02-10 Fix board outline and export gerbers
    [Arm Control Board-B_Cu.gbl, Arm Control Board-B_Mask.gbs, Arm Control Board-B_SilkS.gbo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]
2015-02-18 Add terminating resistance for 485, add 232 header
    Resolves #23 #22
    [Arm Control Board.sch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]
2015-02-18 Add value for terminating resistance on 485
    #24
    [Arm Control Board.sch]
2015-02-19 Improved serial and servo connectors, moved refs
    [7V4 Regulators.sch, Arm Control Board.kicad_pcb, Arm Control Board.sch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]
2015-03-03 Reorganize silkscreen
    [Arm Control Board-B_Cu.gbl, Arm Control Board-B_Mask.gbs, Arm Control Board-B_SilkS.gbo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]
2015-03-03 Add M3 mounting holes
    [Arm Control Board.kicad_pcb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]
2015-03-03 Plate M3 holes
    [Arm Control Board-B_Cu.gbl, Arm Control Board-B_Mask.gbs, Arm Control Board-B_SilkS.gbo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]
2015-03-03 Remove back solder mask from plated holes
    [Arm Control Board.kicad_pcb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]
2015-03-03 Remove front solder mask from plated holes
    [Arm Control Board.kicad_pcb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]
2015-03-03 Add pinout silk screen text. Exports sent to fab
    [Arm Control Board.kicad_pcb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]
2015-03-03 Add some pretty board images
2015-03-05 Assemble BOM for initial order
    [Arm Control Board.csv, Board parts.xlsx]
2015-03-28 Add cat5 jack for ethernet
    [7V4 Regulators.sch, Arm Control Board.sch, Low Voltage Regulators.sch]
